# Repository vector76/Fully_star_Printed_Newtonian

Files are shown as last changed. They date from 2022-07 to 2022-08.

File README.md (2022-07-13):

# Fully* Printed Newtonian
The purpose of this project is to create a low-cost, easy to build, yet high quality starter telescope suitable for beginners, which can be extended with accessories for more advanced stargazing.

The goal is to lower the barrier to entry as much as possible, without sacrificing image quality.

Lowering the barrier to entry is viewed in terms of cost and also minimizing the effort in sourcing materials and assembling.  A parametric design can accommodate many mirror sizes, but depending on the size of mirror that is available (and inexpensive), it may be difficult to purchase a tube of suitable size.  Printing the tube is relatively low-cost, and removes the constraint on finding an existing appropriate tube.  A fully* printed design is not a goal per se, but rather it is a consequence of designing to maximize availability.

Full assembly instructions are available in the included PDF.

The source is being published with a permissive license, and the files are also on Printables.com [here](https://www.printables.com/model/241144).

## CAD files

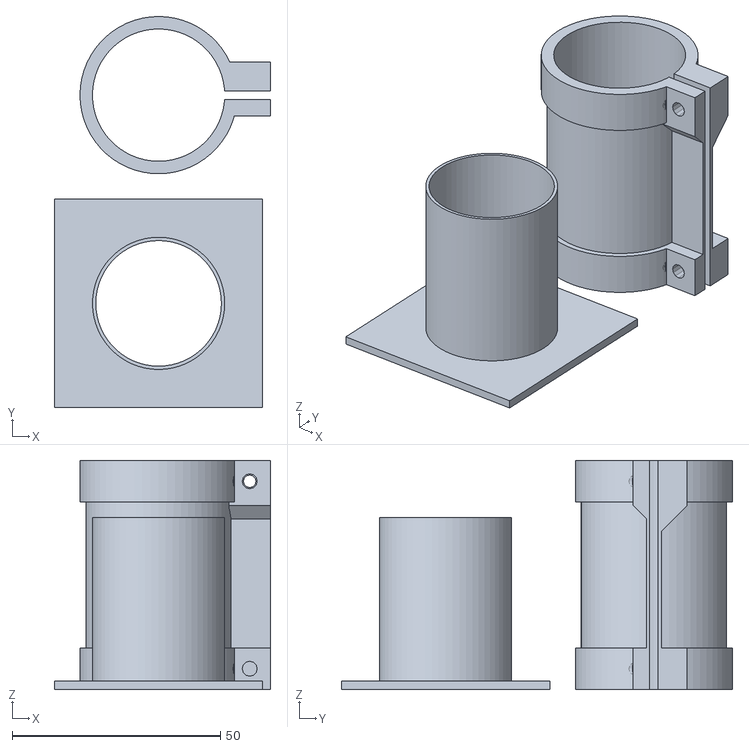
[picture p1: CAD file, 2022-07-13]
Accessories/Focus Estimator.stl
51.9 x 93.9 x 55.0

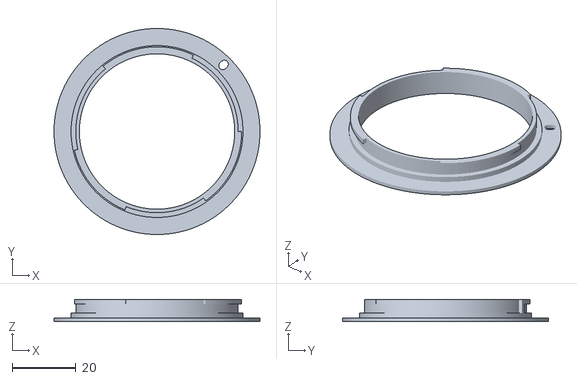
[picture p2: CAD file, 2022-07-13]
Canon_EF_mount_by_thenickdude.stl
64.6 x 64.6 x 6.90

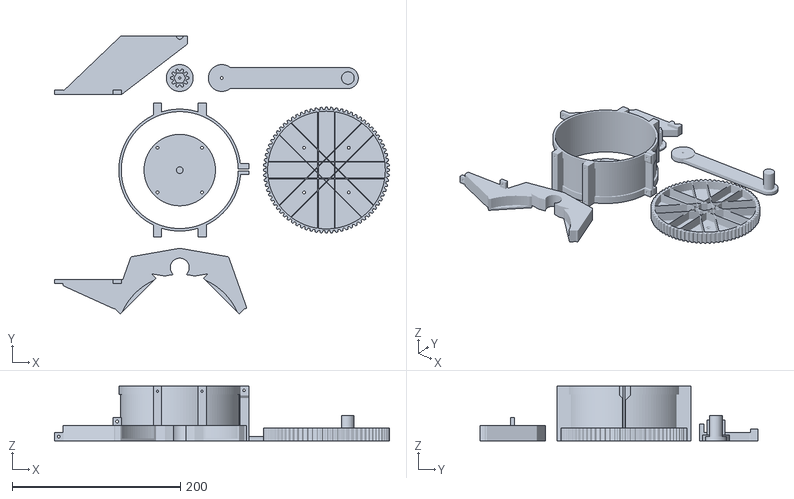
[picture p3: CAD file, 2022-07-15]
D114F900/D114F900 Micro Dobs Print Layout.stl
398.5 x 330.7 x 65.0

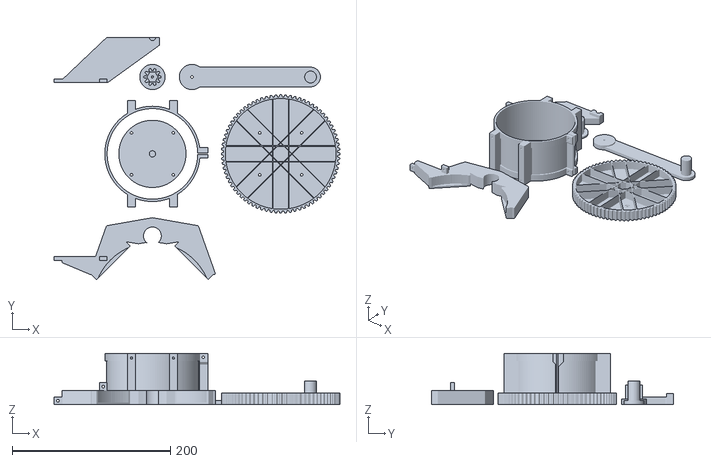
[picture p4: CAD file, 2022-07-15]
D80F800/D80F800 Micro Dobs Print Layout.stl
361.8 x 306.2 x 65.0

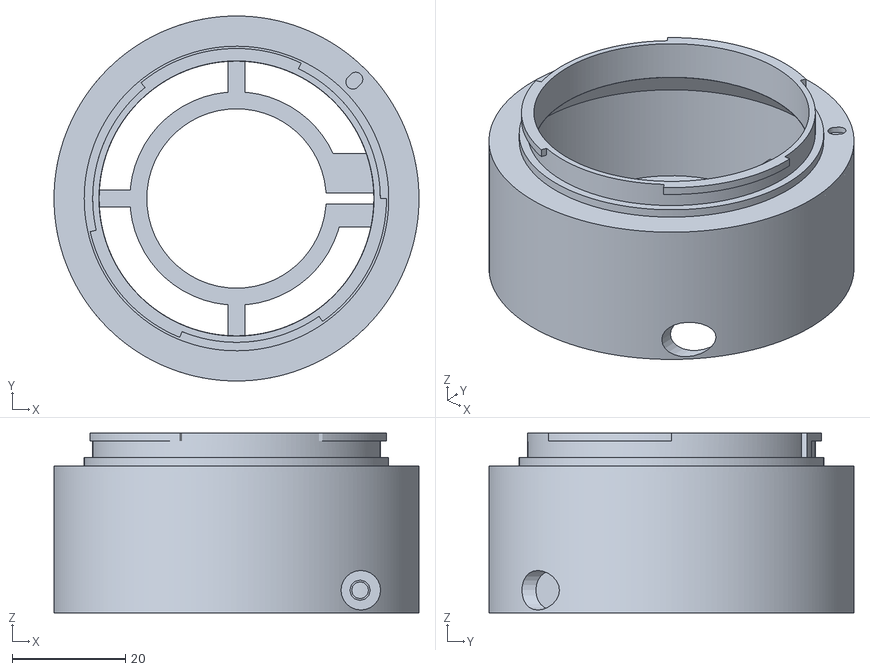
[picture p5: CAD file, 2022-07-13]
Accessories/Canon EF Mount.stl
64.6 x 64.6 x 31.8

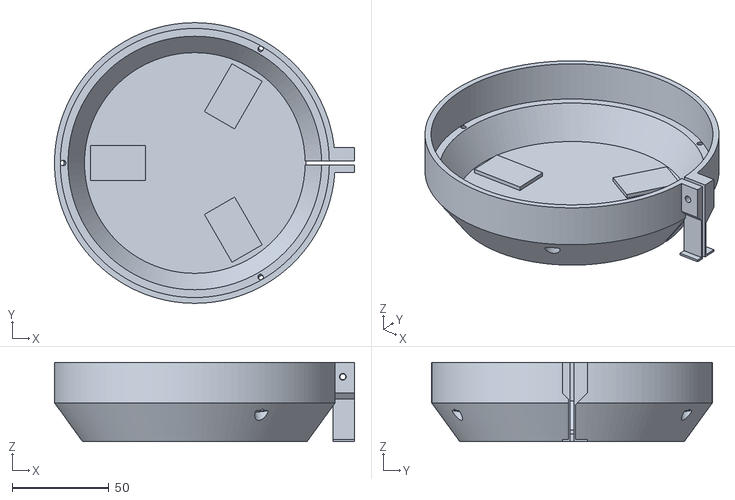
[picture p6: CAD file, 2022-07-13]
D114F900/D114F900 Primary Mount.stl
155.0 x 145.0 x 41.0

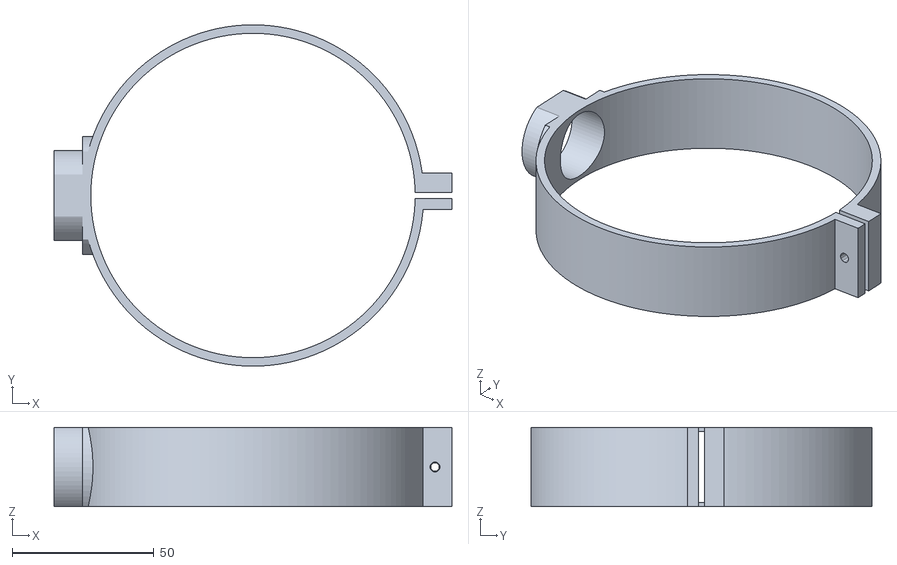
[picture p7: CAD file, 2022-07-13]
D80F800/D80F800 View Mount.stl
140.5 x 120.5 x 28.0

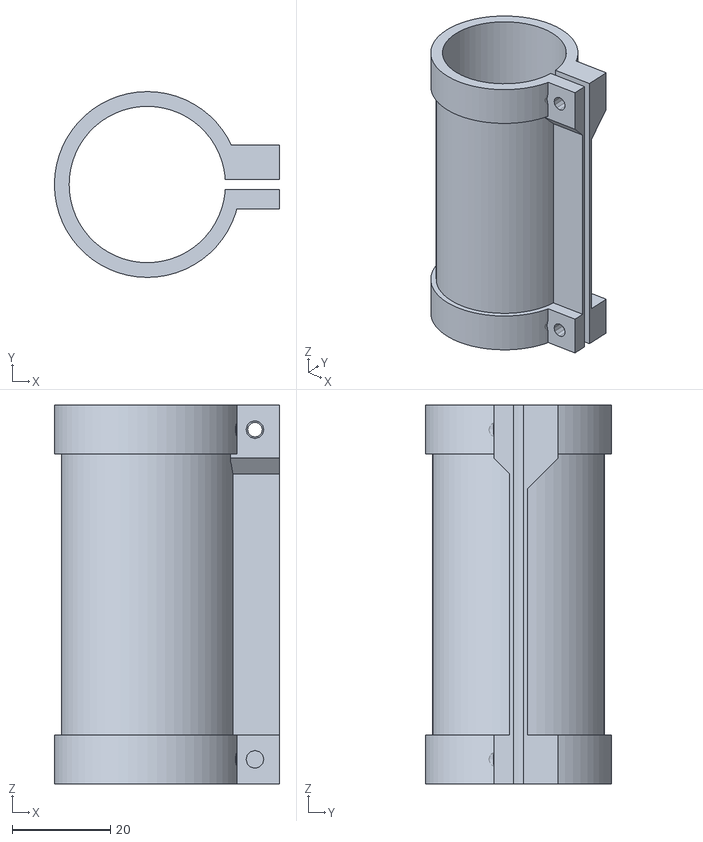
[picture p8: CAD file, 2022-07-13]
Accessories/Eyepiece Mount.stl
45.8 x 37.8 x 77.0

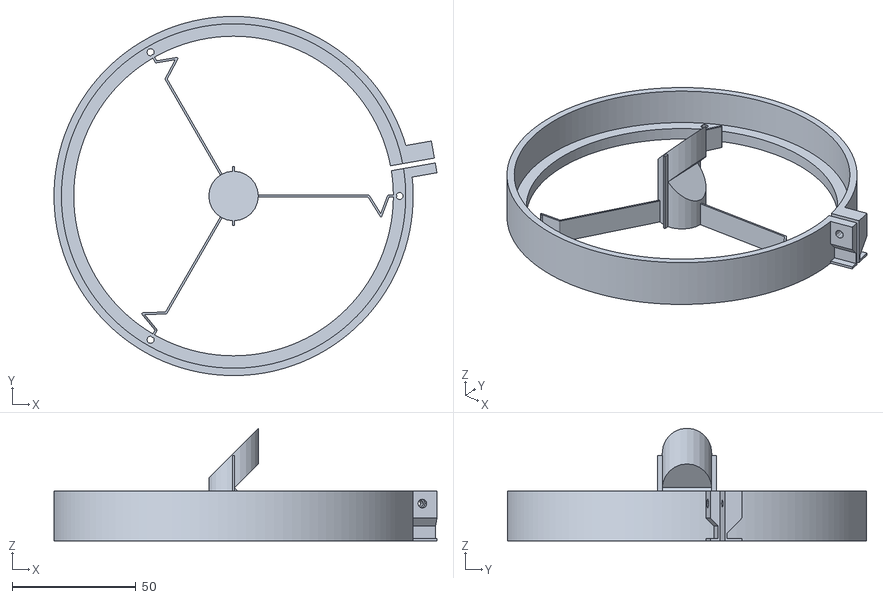
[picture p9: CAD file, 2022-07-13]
D114F900/D114F900 Spider.stl
154.6 x 145.0 x 45.4

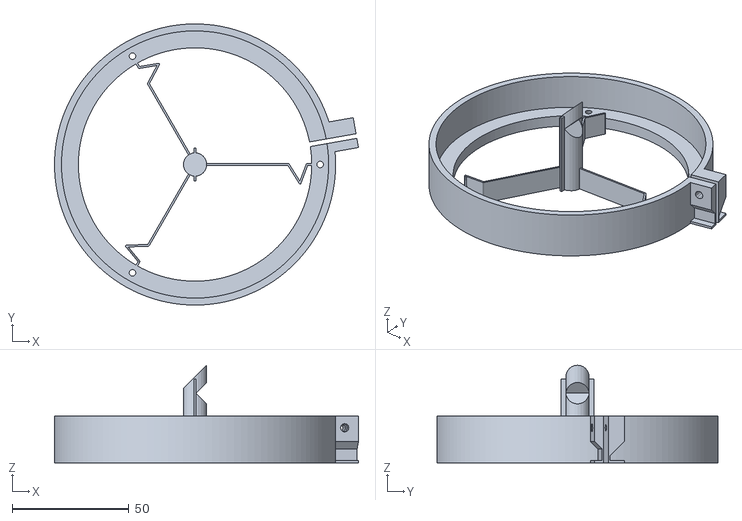
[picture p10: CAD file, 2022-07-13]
D80F800/D80F800 Spider.stl
130.3 x 120.5 x 41.8

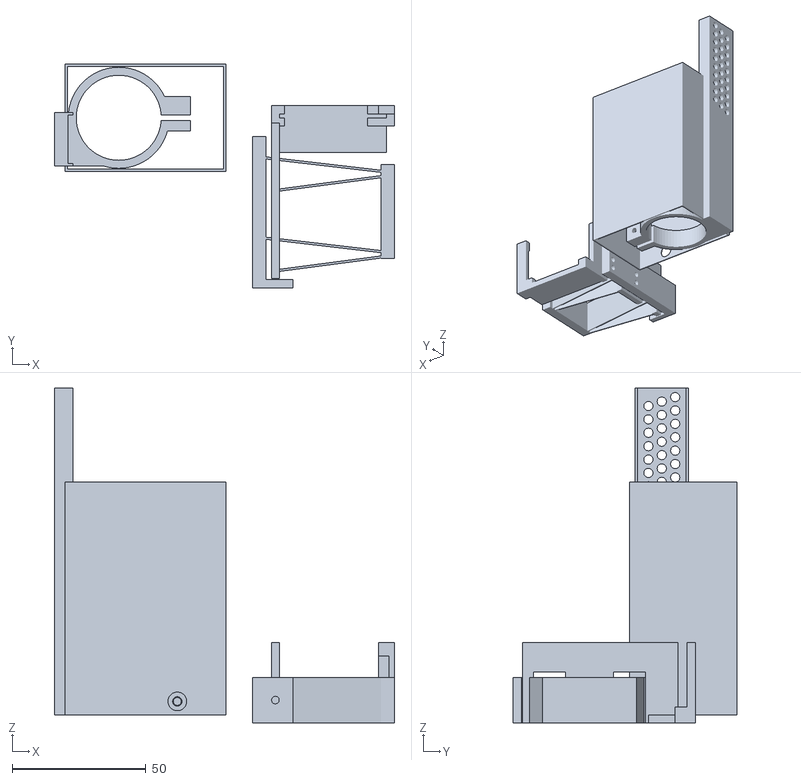
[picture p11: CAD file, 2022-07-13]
Accessories/ESP32-Cam Mount.stl
127.0 x 83.5 x 125.0

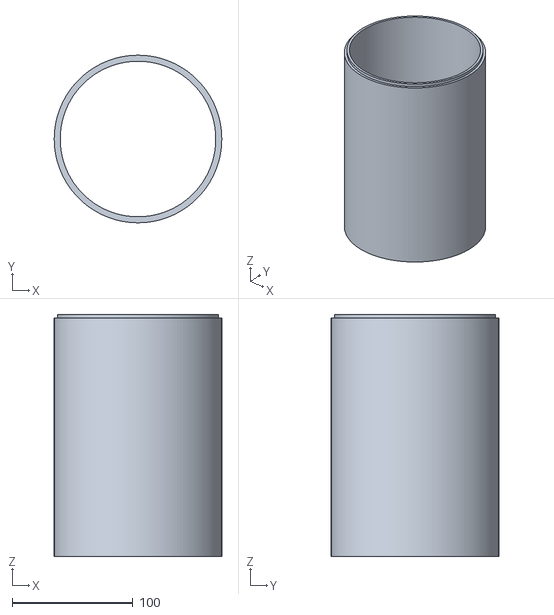
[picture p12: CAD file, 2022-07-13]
D114F900/D114F900 Tube Middle.stl
139.0 x 139.0 x 200.8

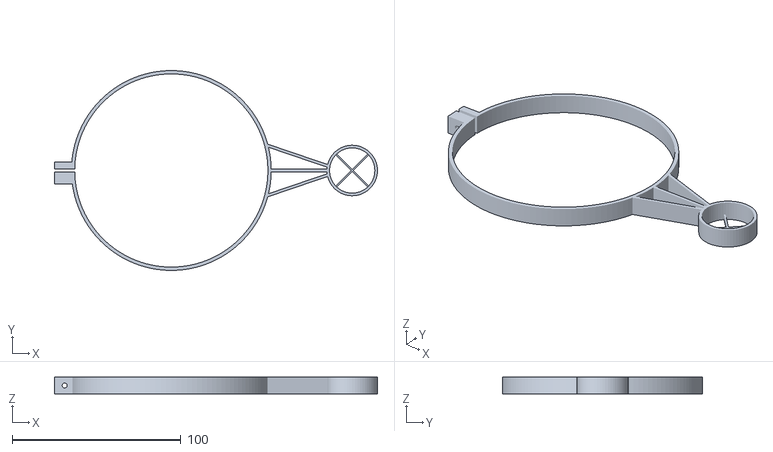
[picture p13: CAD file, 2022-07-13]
D80F800/D80F800 Aiming Reticle.stl
191.5 x 118.5 x 10.0

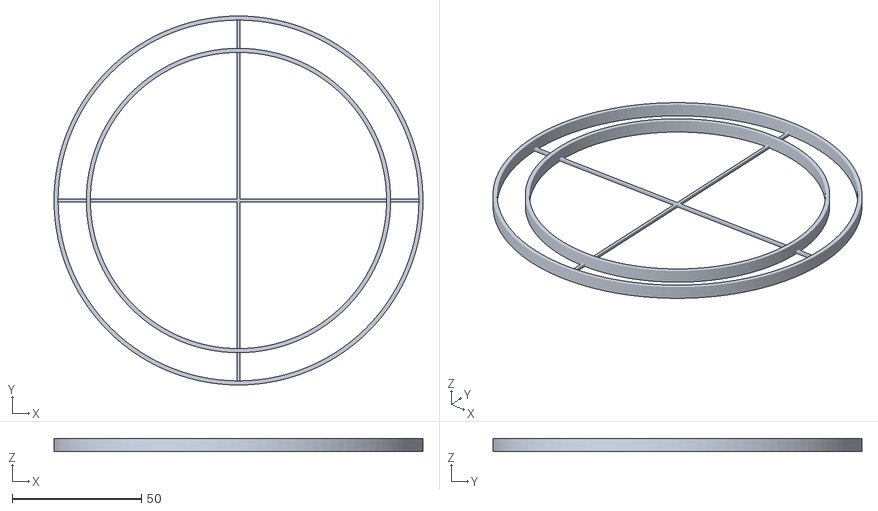
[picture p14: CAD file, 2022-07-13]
D114F900/D114F900 Primary Aligner.stl
142.8 x 142.8 x 5.00

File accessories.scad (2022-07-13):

use <core_parts.scad>  // for ministrap


module primary_crosshairs() {
  wall = 1.6;
  gap = 0.3;
  
  difference() {
    cylinder(d=tube_od+2*gap+2*wall, h=5, $fn=120);
    tz(-0.5) cylinder(d=tube_od+2*gap, h=6, $fn=120);
  }

  // second ring on mirror OD doesn't make a difference with alignment but may be handy
  // for locating the center of the primary.
  difference() {
    cylinder(d=mirror_od+2*gap+2*wall, h=5, $fn=120);
    tz(-0.5) cylinder(d=mirror_od+2*gap, h=6, $fn=120);
  }
  
  for (a=[0, 90]) rotate([0, 0, a])
  tz(0.6) cube([tube_od+1*gap+wall, 1, 1.2], center=true);
}


// secondary crosshairs not really necessary
module secondary_crosshairs() {
  sec_od = 1.25*25.4;
  
  wall = 1.6;
  gap = 0.3;
  
  difference() {
    cylinder(d=sec_od+2*gap+2*wall, h=5, $fn=120);
    tz(-0.5) cylinder(d=sec_od+2*gap, h=6, $fn=120);
  }
  
  for (a=[0, 90]) rotate([0, 0, a])
  tz(0.4) cube([sec_od+1*gap+wall, 1, 0.8], center=true);
}


module EF_mount(clamph=8, mount_depth=ef_mount_depth) {
  efraised = mount_depth-44 - 1;
  // focus is 44.0 mm behind the flange of the mount
  // make it slightly short to allow it to move 1mm closer
  
  // strap
  ministrap(strap_w=clamph);
  // legs
  for (a=[-90, 0, 90]) rotate([0, 0, a]) translate([-32, -1.5, 0]) cube([14, 3, clamph]);

  // ef mount, raised, with a hole for screw access
  difference() {
    EF_mount_raised(h=efraised);
    translate([22, -9, clamph/2]) rotate([90, 0, 0]) cylinder(d=7, h=100, $fn=24);
  }
}


module EF_mount_raised(h=5) {
  wall = 2;
  translate([0, 0, h]) import("Canon_EF_mount_by_thenickdude.stl");

  // slope downward from x=24.3, y=h-1.05 by y=-x+24.3+h-1.05 at x=32.3-wall
  vy = max(0, -32.3+wall+24.3+h-1.05);
  
  difference() {
    union() {
      // %cylinder(d=64.6, h=h-0.95, $fn=120);
      rotate_extrude($fn=200)
      polygon([[32.3-wall, 0], [32.3, 0], [32.3, h-1.05], [24.3, h-1.05], [32.3-wall, vy]]);
    }
    translate([0, 0, -0.5]) cylinder(d=48.6, h=h, $fn=120);
  }
}


module focus_estimator(ht=(mount_length-13)*2/3) {
  w = 0.8;  // thinner than strap so they clamp independently
  tube_d = 25.4*1.25;  // base and eyepiece are same diameter
  
  difference() {
    union() {
      translate([-25, -25, 0]) cube([50, 50, 2]);
      cylinder(d=tube_d, h=ht, $fn=60);
    }
    translate([0, 0, -0.5]) cylinder(d=tube_d-2*w, h=ht+5+1, $fn=60);
  }
}



// work in progress, not ready for release
module eyepiece_fine_adjust(ht=flange_to_focus) {
  // ht is the height above the base where the focus is located
  w = 1.6;  // thinner than strap so they clamp independently
  tube_d = 25.4*1.25;  // base and eyepiece are same diameter
  
  wing_w = 15;
  wing_l = 60+tube_d/2;
  wing_th = 0.6;
  neutral = 6;
  
  // bottom part
  translate([wing_l, wing_l+wing_w+15, 0]) {
    ministrap(id=tube_d);
    
    difference() {
      union() {
        // wings
        for (a=[60, 180, -60]) rotate([0, 0, a]) {
          translate([0, -wing_w/2, 0]) cube([wing_l+1, wing_w, wing_th]);
          // block at end
          translate([wing_l, -wing_w/2, 0]) cube([10, wing_w, neutral+2]);
        }
        // block for deflecting flexure
        rotate([0, 0, -120]) translate([0, -5, 0]) cube([tube_d/2+20, 10, 6]);
      }
      
      // bore out id again
      tz(-0.5) cylinder(d=tube_d, h=11, $fn=60);
      for (a=[60, 180, -60]) rotate([0, 0, a]) {
        // holes in wings
        translate([wing_l+5, 0, -0.5]) cylinder(d=2.9, h=neutral+3, $fn=12);
        // 2mm recess for top part
        translate([wing_l, -5, neutral]) cube([11, 10, 10]);
        translate([wing_l+1-10, -wing_w/2-0.5, neutral]) cube([10, wing_w+1, 10]);
      }
    }
  }
    
  // top part
  // upper strap 10mm shorter than fixed eyepiece
  translate([0, 0, ht-5-10]) ministrap(id=tube_d, feetht=support_free ? ht-5-10 : 0);
  
  // wings and 
  difference() {
    union() {
      // tube
      cylinder(d=tube_d+2*w, h=ht+5-10, $fn=60);
      // bottom reinforcement
      cylinder(d=tube_d+6, h=3, $fn=60);
      // wings
      for (a=[60, 180, -60]) rotate([0, 0, a]) {
        // flexure
        translate([0, -wing_w/2, 0]) cube([wing_l+1, wing_w, wing_th]);
        // block at end for attachment
        translate([wing_l, -10/2, 0]) cube([10, 10, 5]);
      }
      // block for deflecting flexure
      rotate([0, 0, -120]) translate([0, -5, 0]) cube([tube_d/2+20, 10, 6]);
    }
    // bore out inside diameter
    translate([0, 0, -0.5]) cylinder(d=tube_d, h=ht+5+1, $fn=60);
    // cut strap
    strap_slice(ht=ht+5+1);
    // holes in wings
    for (a=[60, 180, -60]) rotate([0, 0, a]) translate([wing_l+5, 0, -0.5]) cylinder(d=3.5, h=6, $fn=12);
    // hole for deflecting flexure
    rotate([0, 0, -120]) translate([tube_d/2+15, 0, -0.5]) cylinder(d=2.9, h=10, $fn=12);
  }
}


module esp32_cam_adapter_mount(nominal_ht=mount_length-3) {
  tube_d = 25.4*1.25;  // base diameter
  hole_offset = 8;  // shift holes to the side
  sup_w = 17;
  tower_ht = nominal_ht + 50;
  
  // strap to grab view mount boss
  ministrap(id=tube_d);
  
  // tower and rectangluar light baffle
  difference() {
    union() {
      // tower
      translate([-19-5, -20/2-hole_offset, 0]) {
        cube([5, 20, tower_ht]);  // main tower
        cube([20, 20, 10]); // foot connection to ministrap
        // guides to prevent offset installlation
        for (y=[0, 19]) translate([0, y, 0]) cube([7, 1, tower_ht]);
      }
      // baffle
      for (x=[-20, 40-0.8]) translate([x, -20, 0]) cube([0.8, 40, nominal_ht+15]);
      for (y=[-20, 20-0.8]) translate([-20, y, 0]) cube([60, 0.8, nominal_ht+15]);
    }
    
    // perforations
    for (yi=[-1, 0, 1])
    for (z=[nominal_ht:5:tower_ht-5])
    translate([-19-6, yi*5-hole_offset, z+yi*5/3]) rotate([0, 90, 0]) 
    cylinder(d=3.5, h=12, $fn=12);

    // bore out space for boss again
    translate([0, 0, -0.5]) cylinder(d=tube_d, h=26, $fn=60);
    
    // access hole for screw
    translate([tube_d/2+6, 0, 5]) rotate([90, 0, 0]) cylinder(d=7, h=50, $fn=30);
  }
  
  %translate([0, 0, nominal_ht]) rotate([-90, 0, 0]) translate([-9, -4, -27/2]) esp32_cam_adapter_flexure();
}


module esp32_cam_adapter_flexure() {
  ht=30;
  tube_d = 25.4*1.25;  // base diameter
  cam_w = 27;
  cam_l = 40;
  cam_ypos = 9;  // camera center is 9mm from one end, centered along width
  
  cam_th = 1.5;
  slot_depth = 3;
  slot_end = 2;
  slot_end2 = 7;
  flex_th = 0.8;
  
  sup_w = 17;
  flex_ht = sup_w; // cam_w/2;
  flex_x = cam_l-2;
  
  hole_offset = 8;  // shift holes downward
  
  // bottom below camera
  translate([0, -3-10, -3]) cube([cam_l, 10+6+cam_th, 3]);
  
  difference() {
    union() {
      translate([-3, -3, -3]) cube([3+slot_end, 6+cam_th, 3+slot_depth]);
      translate([cam_l-slot_end2,-3,-3]) cube([slot_end2+3, 6+cam_th, 3+slot_depth]);
    }
    cube([cam_l, cam_th, cam_w]);
  }
  
  // vertical stem
  translate([cam_l-3, cam_th, 0]) difference() {
    cube([6, 3, cam_w]);
    // cavity so it doesn't jam in the middle and skew it
    translate([-0.1, -0.5, 3]) cube([4, 1.5, cam_w-8]);
  }
  
  // intermediate
  translate([flex_x, -50-2.5, -3]) cube([5, 35, flex_ht]);
  
  for (y=[-20, -50]) {
    // stage 1 flexures
    hull() {
      translate([flex_x, y, -3]) cylinder(d=flex_th, h=flex_ht, $fn=36);
      translate([-5, y+5, -3]) cylinder(d=flex_th, h=flex_ht, $fn=36);
    }
    
    // stage 2 flexures
    hull() {
      translate([flex_x, y-2, -3]) cylinder(d=flex_th, h=flex_ht, $fn=36);
      translate([0, y-7, -3]) cylinder(d=flex_th, h=flex_ht, $fn=36);
    }
  }
  
  // final stage of flexure?
  difference() {
    translate([-3, -50-10, -3]) cube([3, 58, cam_w+3]);
    for (y=[-20, -50]) translate([-3.5, y-6, -3.1]) cube([6, 12, flex_ht+2.1]);
  }
  
  // support and holes for mounting screw
  difference() {
    translate([-10, -62, -3]) cube([5, 55, sup_w]);
    for (zi=[-1, 0, 1])
    for (y=[-30, -10]) translate([-11, y, cam_w/2+zi*5-hole_offset]) 
      rotate([0, 90, 0]) cylinder(d=2.9, h=12, $fn=12);
  }
  
  // top ledge and spot for focus adjustment screw
  translate([-10, -62-1.5, -3])
  difference() {
    cube([15, 3, sup_w]);
    translate([8.5, -1, flex_ht/2]) rotate([-90, 0, 0]) cylinder(d=2.9, h=10, $fn=12);
  }
  
  
  // top diving board and focus adjustment screw
  *difference() {
    translate([-10, -55-5, -3]) cube([cam_l+10+2+5, 5, cam_w-1]);
  
    translate([cam_l+2+2.5, -61, (cam_w-1)/2-3])
    rotate([-90, 0, 0]) cylinder(d=2.9, h=12, $fn=12);
  }
  
  // visualize board and camera
  %cube([cam_l, cam_th, cam_w]);
  %translate([cam_ypos, cam_th, cam_w/2]) 
  rotate([-90, 0, 0]) cylinder(d=8, h=8, $fn=24);
  
  // from center of camera to surface of support plate is 19 mm.
  // focal plane is about 4mm from back surface
  // so focal plane to mounting hole is about 34 mm
  // with focus about 30mm above base, we need 64 mm from base to mounting hole

}

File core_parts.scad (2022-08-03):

module assembled() {
  %cylinder(d=tube_od, h=tube_length);
  primary_mount();
  
  translate([0, 0, tube_length/2]) rotate([0, 0, 180]) tripod_strap();
  
  tz(tube_length) rotate([180, 0, 0]) spider();
  
  tz(secondary_distance-7.5-primary_setback) image_base_strap();
  
  for (z=[tube_length*0.1, tube_length*0.7])
  tz(z) rotate([0, 0, 140]) test_strap_aiming();
}


module all_part_layout() {
  layout = tube_od+15;

  translate([0, 0, mirror_thickness+7])
  r45() primary_mount();

  translate([0, layout, 5]) r45() spider();

  translate([-layout, 0, 12.5]) r45() tripod_strap();

  // for testing strap design and fit with OD
  // translate([layout, 0, 0]) r45() test_strap_aiming();

  translate([-layout, layout, 0]) r45() image_base_strap();

  translate([-layout, layout, 0]) eyepiece_tube();
}


module eyepiece_tube(ht=flange_to_focus, extra=0) {
  // ht is the height above the base where the focus is located
  w = 1.6;  // thinner than strap so they clamp independently
  tube_d = 25.4*1.25;  // base and eyepiece are same diameter
  
  // two straps
  ministrap(id=tube_d);
  translate([0, 0, ht-5]) ministrap(id=tube_d, feetht=support_free ? ht-15 : 0);
  
  // tube to connect them
  difference() {
    cylinder(d=tube_d+2*w, h=ht+5+extra, $fn=60);
    translate([0, 0, -0.5]) cylinder(d=tube_d, h=ht+5+extra+1, $fn=60);
    strap_slice(ht=ht+5+extra+1);
  }
  
}


module ministrap(id=25.4*1.25, wall=3, strap_w=10, slice_w=2, feetht=0) {
  feetw = 0.8;
  difference() {
    union() {
      cylinder(d=id+2*wall, h=strap_w, $fn=60);
      
      difference() {
        // block for clamping
        translate([id/2+wall-2, -5, -feetht])
          cube([10, 13, strap_w+feetht]);
        
        // remove feetht from bottom but only from the clamping block
        if (feetht > 0) {
          hull() for (dy=[0, 10])
          translate([id/2+wall-2.5, slice_w/2+feetw+dy, -feetht-dy-20])
          cube([13, 1, feetht+2*dy-7+20]);
          
          mirror([0, 1, 0]) hull() for (dy=[0, 10])
          translate([id/2+wall-2.5, slice_w/2+feetw+dy, -feetht-dy-20])
          cube([13, 1, feetht+2*dy-4+20]);
        }
      }
    }
    
    // bore
    translate([0, 0, -0.5]) cylinder(d=id, h=strap_w+1, $fn=60);
    
    // slice for clamping
    strap_slice(ht=strap_w+1+feetht, slice_w=slice_w);
    
    // screw holes for clamping
    translate([id/2+wall+3, 0, strap_w/2]) {
      rotate([90, 0, 0]) cylinder(d=3.6, h=12, $fn=12);
      rotate([-90, 0, 0]) cylinder(d=3, h=12, $fn=12);
      translate([0, -5.1, 0]) rotate([90, 0, 0]) cylinder(d=8, h=12, $fn=24);
    }    
  }
  
}


module r45() {
  rotate([0, 0, 45]) children();
}


module image_base_strap() {
  //sw = 15;  // width of thick part of strap
  //tw = 6;  // extra thin width added top and bottom
  sw = 28;
  tw = 0;
  st = 3;  // strap thickness (thick part)
  tl = 10;  // part of tube for grabbing
  
  difference() {
    union() {
      strap(wall=st, strap_w=sw, thinbot=tw, feetht=support_free ? tw : 0);
  
      translate([-tube_od/2-10-st, 0, sw/2])
      rotate([0, 90, 0]) {
        cylinder(d=31.75, h=tl+st, $fn=60);
        // flange provides decent flat surface rather than relying on tube od
        translate([0, 0, tl]) cylinder(d=41.75, h=st+5, $fn=60);
      }
    }
    
    // inside tube bore
    translate([0, 0, -tw-0.5]) cylinder(d=tube_od, h=sw+2*tw+1, $fn=120);
    
    // bore in tube
    translate([-tube_od/2-10-4, 0, sw/2]) 
    rotate([0, 90, 0])  cylinder(d=25, h=20, $fn=60);
    
    // cut off top and bottom
    for (z=[sw+tw, -50-tw]) translate([0,0,z]) cylinder(d=tube_od+2*tl+2*st+10, h=50);
  }
  
  %translate([-tube_od/2-3, 0, sw/2]) rotate([0, -90, 0]) eyepiece_tube();
}


module test_strap_aiming() {
  dist = 50;  // distance from OD of tube
  rib_w = 1.6;
  ring_od = 30;
  ring_r = ring_od/2;
  ring_th = 1.6;
  
  rotate([0, 0, 180]) strap(wall=2);
  
  difference() {
    union() {
      // three ribs support the ring
      for (a=[0, 15, -15]) hull() {
        rotate([0, 0, a]) 
        translate([tube_od/2+1, 0, 0]) cylinder(d=rib_w, h=10, $fn=24);
        translate([tube_od/2+dist-ring_r+1, a/6, 0]) cylinder(d=rib_w, h=10, $fn=24);
      }
      
      translate([tube_od/2+dist, 0, 0])
      cylinder(d=ring_od, h=10, $fn=60);
    }
    
    translate([tube_od/2+dist, 0, -0.5])
    cylinder(d=ring_od-2*ring_th, h=11, $fn=60);
  }
  
  // crosshairs
  translate([tube_od/2+dist, 0, 0]) for (a=[-45, 45]) rotate([0, 0, a])
  translate([-ring_r, -0.4, 0]) cube([ring_od, 0.8, 3]);
}

module strap_slice(ht=11, slice_w=2) {
  // slice ring and maybe other stuff
  translate([0, -slice_w/2, -ht]) cube([300/2+21, slice_w, 2*ht]);
}


module strap(wall=3, strap_w=10, clamp_extra=0, slice_w=2, extrabot=0, thinbot=0, feetht=0) {
  strap_mid = strap_w/2;
  thinw = 0.8;
  feetw = 0.8;
  
  // main strap
  difference() {
    union() {
      // main ring grips outside of tube
      hull() {
        translate([0, 0, -extrabot])
        cylinder(d=tube_od+2*wall, h=strap_w+extrabot, $fn=120);
      
        if (thinbot > 0) translate([0, 0, -extrabot-wall])
        cylinder(d=tube_od+2*thinw, h=strap_w+extrabot+2*wall, $fn=120);
      }
      
      if (thinbot > 0)
        translate([0, 0, -thinbot])
        cylinder(d=tube_od+2*thinw, h=strap_w+2*thinbot, $fn=120);
      
      difference() {
        // block for clamping, 5 one side, 8 other side, not counting slice
        translate([tube_od/2+wall-1, -5-clamp_extra, -feetht]) 
          cube([11, 13+clamp_extra, strap_w+feetht]);

        // remove feetht from bottom but only from the clamping block
        if (feetht > 0) {
          hull() for (dy=[0, 10])
          translate([tube_od/2+wall-1.5, slice_w/2+feetw+dy, -feetht-dy-20])
          cube([12, 1, feetht+2*dy-7+20]);
          
          mirror([0, 1, 0]) hull() for (dy=[0, 10])
          translate([tube_od/2+wall-1.5, slice_w/2+feetw+dy, -feetht-dy-20])
          cube([12, 1, feetht+2*dy-4+20]);
        }
      }
      
      if (feetht > 0) {
        translate([tube_od/2+wall-1, -5, -feetht]) 
        cube([11, 13, 1]);
      }
    }

    // bore for tube
    translate([0, 0, strap_mid-extrabot/2]) {
      cylinder(d=tube_od, h=strap_w+extrabot+2*thinbot+1, center=true, $fn=120);
    }

    // slice for clamping
    strap_slice(ht=strap_w+1+thinbot+extrabot+feetht, slice_w=slice_w);

    // screw holes for clamping
    translate([tube_od/2+wall+4, 0, strap_mid]) {
      rotate([90, 0, 0]) cylinder(d=3.6, h=12, $fn=12);
      rotate([-90, 0, 0]) cylinder(d=3, h=12, $fn=12);
      translate([0, -5.1, 0]) rotate([90, 0, 0]) cylinder(d=8, h=12, $fn=24);
    }
    
  }
}


module tripod_strap() {
  wall = 3;
  strap_w = 15;
  strap_mid = strap_w/2;
  block_len = 40;
  block_w = 39;
  block_th = 6.8;  // about 1.2 mm thick behind nut
  clamp_extra = 2;
  
  botamt = (block_len-strap_w)/2;
  
  difference() {
    union() {
      // strap included so bolt can be subtracted also
      rotate([0, 0, 130])
      strap(strap_w=strap_w, clamp_extra=clamp_extra, thinbot=botamt, feetht=support_free ? botamt : 0);
  
      // tripod block (silghtly wide to attach other blocks
      translate([-block_th-tube_od/2, -block_w/2-0.5, -block_len/2+strap_mid])
      cube([block_th+5, block_w+1, block_len]);
      
      *for (i=[0,1]) mirror([0, i, 0])
      translate([-tube_od/2-block_th-4, block_w/2, -block_len/2+strap_mid])
      cube([14, 3, block_len]);
    }
    
    // bore for tube (leaves material at ends of tripod block)
    translate([0, 0, strap_mid]) {
      cylinder(d=tube_od, h=block_len-8, center=true, $fn=120);
      cylinder(d=tube_od-0.6, h=block_len+1, center=true, $fn=120);
    }
    
    // pocket for 1/4-20 nut
    translate([-tube_od/2-5.6, 0, strap_mid]) rotate([0, 90, 0])
    cylinder(d=12.9, h=10, $fn=6);  // plenty tall, reaches inward
    
    // hole for 1/4-20 screw
    translate([-tube_od/2-block_th-0.5, 0, strap_mid]) rotate([0, 90, 0])
    cylinder(d=25.4/4, h=block_th+5, $fn=24);
    
  }
}


// front end holds secondary mirror
module spider() {
  stem_length = hole_from_end-secondary_thickness*sqrt(2);
  stem_d = secondary_size-5;
  spar_w = 0.8;
  base = 5;

  // strap for grabbing tube, extends downward to join with additional ring
  rotate([0, 0, 10])
  tz(5) strap(extrabot=base+5, feetht=support_free ? 5+5 : 0);
  
  difference() {
    translate([0, 0, -base]) cylinder(d=tube_od+1, h=base, $fn=120);
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

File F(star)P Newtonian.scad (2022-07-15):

// Which part(s) to show
part = "Assembled";  // [ "Primary Mount", "Spider", "View Mount", "Tripod Strap", "Assembled", "Parts Flat", "Primary Aligner", "Aiming Reticle", "Eyepiece Mount", "Canon EF Mount", "Focus Estimator", "ESP32-Cam Mount", "Tube Bottom", "Tube Middle", "Tube Top", "Tube Demonstration", "Micro Dobs Assembled", "Micro Dobs Print Layout" ]
// Diameter of primary mirror (mm)
mirror_od = 114;
// Focal length (mm)
mirror_focal_length = 900;
// Thickness of primary mirror (mm)
mirror_thickness = 14; // 0.1
// Minor diameter of secondary mirror (mm)
secondary_size = 25;
// Thickness of secondary mirror (mm)
secondary_thickness = 5; // 0.1
// Purchased tube or printed?
tube_source = "Printed"; // [ Printed, Purchased ]
// Adjust model so supports are mostly unnecessary?
support_free = true;

/* [Printed Tube Options] */
// Maximum Z height of tube segments (mm)
max_print_ht = 210;

/* [Purchased Tube Parameters] */
// Inside diameter of purchased tube (mm)
purchased_tube_id = 89.2;
// Outside diameter of purchased tube (mm)
purchased_tube_od = 76.3;

module customizer_stop() {}

/* [Accessory Parameters] */
// Flange to focal distance
ef_mount_depth = 71; // 0.1

// Common variables for both tube and parts
part2 = "";
part_ = part2 == "" ? part : part2;  // override part with part2

// intended size of output projected image (magnification depends on focal length)
fov_size = 15;
// tube must be larger than mirror or it will block some of field of view
tube_id = tube_source == "Purchased" ? purchased_tube_id : mirror_od + fov_size;
// outer diameter
tube_od = tube_source == "Purchased" ? purchased_tube_od : tube_id + 2*5;
// thickness of tube wall
tube_wall = (tube_od-tube_id)/2;
// front of primary is this far back from end of tube (for length purposes)
primary_setback = 2;
// the strap for attaching stuff is this wide
mount_strap_width = 35;
// in front of mount strap, leave this much for the spider to grab onto
spider_clip_allowance = 20;
// center of side hole distance from tube front end
hole_from_end = spider_clip_allowance + mount_strap_width/2;
// size of hole matches mount strap
hole_size = 25;
// focus is this radial distance from outside of tube
mount_length = 75;
// focus is this distance from center of tube
focus_total_radius = mount_length + tube_wall + tube_id/2;
// distance from primary mirror to center of secondary
secondary_distance = mirror_focal_length - focus_total_radius;
// total tube length after assembly
tube_length = secondary_distance - primary_setback + mount_strap_width/2 + spider_clip_allowance;
// distance from mounting flange to focal plane (3 is thickness of flange)
flange_to_focus = mount_length - 3;

// These items are specific to the tube generation:

// joint between tubes overlaps by this much (tiny bit needed just for alignment)
joint_overlap = 3;
// number of tube sections given maximum printable Z
tube_sections = ceil(tube_length / (max_print_ht-joint_overlap));
// section effective length (excludes overlap)
section_effective_length = tube_length/tube_sections;
// number of facets (and internal corrugations)
p = floor(tube_id*PI/(tube_wall-1.2)*sqrt(2)/2)*2;

// Guidance for the user, printed or purchased:

echo("###########################################");
if (tube_source == "Purchased") {
  echo(str(" Cut tube to length: ", str(tube_length), " mm"));
  echo(str(" Hole center this far from end: ", str(mount_strap_width/2+spider_clip_allowance), " mm"));
  echo(str(" Hole diameter: ", str(hole_size), " mm"));
}
else {
  echo(str(" Printed tube total length: ", tube_length, " mm"));
  echo(str(" Printed tube outside diameter: ", tube_od, " mm"));
  echo(str(" Printed tube section height (excluding top lip):", section_effective_length, " mm"));
  echo(str(" Total number of tube segments: ", tube_sections));
}
echo("###########################################");

// Implementation below here
include <tube_modules.scad>
include <core_parts.scad>
include <accessories.scad>
include <micro_dobs_mount.scad>

// Core parts
if (part_ == "Primary Mount") { primary_mount(); }
if (part_ == "Spider") { spider(); }
if (part_ == "View Mount") { image_base_strap(); }
// Additional parts for main tube
if (part_ == "Tripod Strap") { tripod_strap(); }
if (part_ == "Alignment Guide") { test_strap_aiming(); }
// Some layouts/visualization?
if (part_ == "Assembled") { rotate([0, 45, 0]) tz(-tube_length/2) assembled(); }
if (part_ == "Parts Flat") { all_part_layout(); }
// Accessories
if (part_ == "Primary Aligner") { primary_crosshairs(); }
if (part_ == "Aiming Reticle") { test_strap_aiming(); }
// if (part == "Secondary Aligner") { secondary_crosshairs(); }
if (part_ == "Focus Estimator") { translate([0, 50, 0]) eyepiece_tube(ht=mount_length*2/3);  
    focus_estimator(); }
if (part_ == "Eyepiece Mount") { eyepiece_tube(); }
//if (part == "Eyepiece Mount w/ Fine Adjustment") { eyepiece_fine_adjust(); }
if (part_ == "Canon EF Mount") { EF_mount(); }
if (part_ == "ESP32-Cam Mount") { esp32_cam_adapter_mount(); 
  translate([60, 0, 0]) esp32_cam_adapter_flexure(); }
// Printed tubes
if (part_ == "Tube Top") { tube_top(); }
if (part_ == "Tube Middle") { tube_mid(); }
if (part_ == "Tube Bottom") { tube_bot(); }
if (part_ == "Tube Demonstration") { difference() { tube_bot(50); tz(25) cylinder(d=500, h=500); } }
// "Micro Dobsonian" mount
if (part_ == "Micro Dobs Assembled") { micro_dobs_assembled(); }
if (part_ == "Micro Dobs Print Layout") { micro_dobs_print_layout(); }

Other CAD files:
D80F800/D80F800 Primary Aligner.stl
D114F900/D114F900 Tripod Strap.stl
D80F800/D80F800 Tripod Strap.stl
D114F900/D114F900 Aiming Reticle.stl
micro_dobs_mount.scad
D114F900/D114F900 Tube Bottom.stl
D114F900/D114F900 Tube Top.stl
D114F900/D114F900 View Mount.stl
D80F800/D80F800 Primary Mount.stl
tube_modules.scad
unwin_modules.scad

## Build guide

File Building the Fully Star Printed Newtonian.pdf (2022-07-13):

# Building the Fully* Printed Newtonian

## Introduction

This document describes the process for selecting sizes and building the “Fully* Printed Newtonian” telescope, which built with only printer filament, mirrors, glue, and #6 screws. (Use of a purchased tube is also an option and is described below.)

The design philosophy and the reasons for certain design choices
are detailed elsewhere, and this document focuses on preparing
the materials, choosing the size, and assembling the telescope.

(The model files are available on Printables.com here (https://www.printables.com/model/241144) and on GitHub here.) (https://github.com/vector76/Fully_star_Printed_Newtonian)

## Materials Required

The printed parts excluding the tube require roughly 250 g of filament (for a 114 mm mirror diameter), at ~100 for the primary mount, and ~50g each for the secondary mount, the viewport mount, and the tripod strap. A bit more will be needed for the various accessories. Black filament should be used to minimize
stray light, although non-black filament may be okay if the
telescope is used only at night.

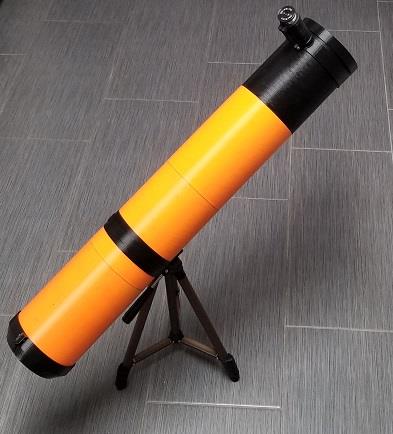
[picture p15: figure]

The tube, if printed, requires about 800 g of filament for the variant with 114 mm diameter, 900 mm focal length. The filament requirement will be roughly proportional to diameter and length. As with the other parts, the tube should be printed with black filament, although it is also possible to paint the interior of the tube.

Excluding the mirror and tube, which are discussed in the next section, you will need:
- Screws: #6 sheet metal screws, 1/2” length, which I believe is equivalent to 3.5 mm sheet metal screws with 12 mm length (length is not critical). You will need at least 6 to install an eyepiece.
- Epoxy
- Tape (optional) for securing mirrors to mounts instead of epoxy

*
Since the Fully* Printed Newtonian is not literally, fully printed, please do not refer to it as “Fully Printed Newtonian” or “FP Newtonian” or “FPN”. Instead call it “Fully* Printed Newtonian” or “F*P Newtonian”, or “F*PN”.

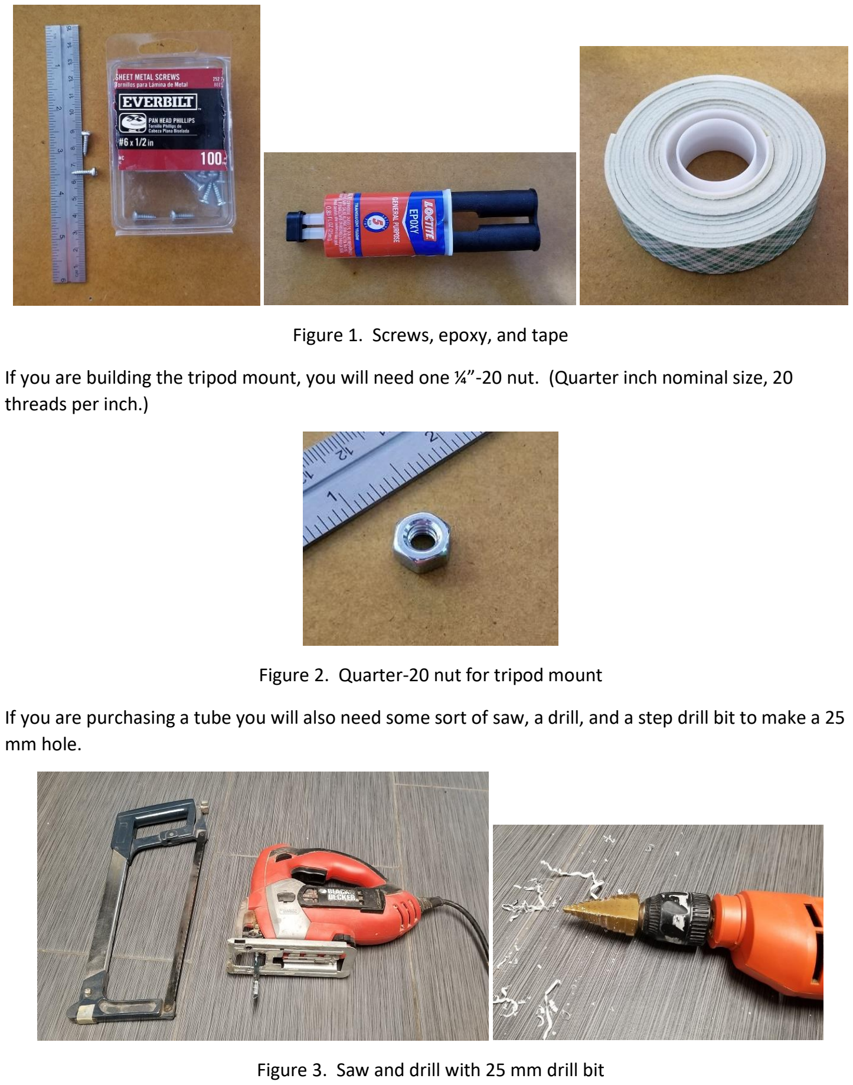
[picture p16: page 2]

Figure 1. Screws, epoxy, and tape

If you are building the tripod mount, you will need one ¼”-20 nut. (Quarter inch nominal size, 20 threads per inch.)

Figure 2. Quarter-20 nut for tripod mount

If you are purchasing a tube you will also need some sort of saw, a drill, and a step drill bit to make a 25 mm hole.

Figure 3. Saw and drill with 25 mm drill bit

## Choice of Mirror and Tube

For a Newtonian style telescope to have ideal performance, there are two options: the primary mirror can be spherical with a relatively long focal ratio, or it must be parabolic. The options are summarized in Figure 4, where the green region represents the zone where spherical mirrors produce good image quality:

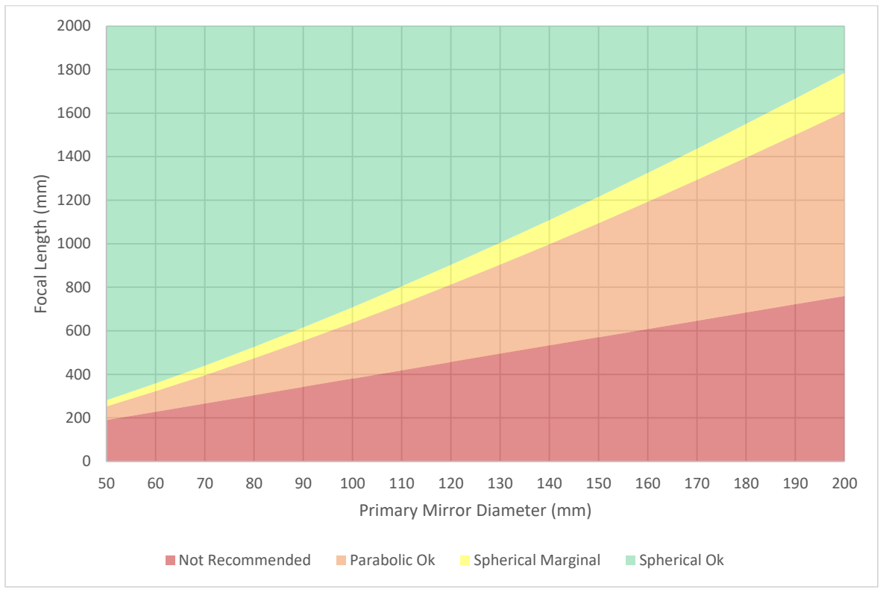
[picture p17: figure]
Focal Length (mm); Primary Mirror Diameter (mm); Not Recommended; Parabolic Ok; Spherical Marginal; Spherical Ok

Figure 4. Cheaper spherical mirrors are permitted at longer focal ratios, while parabolic mirrors are required for shorter focal ratios.

Since spherical mirrors are much less expensive than parabolic mirrors, it is assumed that spherical mirrors with long focal lengths are usually going to be chosen, but parabolic mirrors are also permitted, except that very short focal lengths are not recommended, as illustrated by the red area in Figure 4.

For a printed tube, the outside diameter of the tube is about 25 mm larger than the mirror, and your printer must be able to accommodate this, plus an additional 6 mm for the various straps that clamp onto to the outside of the tube. So, for example, a 150 mm printable area would be able to accommodate a mirror size up to 119 mm.

If you purchase a tube, the recommended size for the inside diameter is between 15 mm and 40 mm larger than the mirror. The exact dimension is not critical, but too large or too small and the performance will suffer. The outside diameter of the tube must be at least 10 mm larger than the diameter of the mirror, or it will not assemble properly.

Given these guidelines, you may purchase a tube and cut it to length if you can find a compatible tube and mirror combination of appropriate sizes, or if you wish to use a mirror for which no appropriate tube can be found (or if you prefer not to use a saw and drill), then you may print a tube instead.

## Constructing Telescope Body from Purchased Tube

Cut the tube such that the length L is

L = focal length − 77 −

tube outside diameter
2

Cut the ends perpendicular and flat to the extent possible. (Note: do not assume the factory-cut end of PVC tube is cut square!) One way to get a square cut is to wrap a ribbon or some flat material like paper around the tube and use it as a guide to mark a line. Then cut the tube very slightly long and use a file or sandpaper to file the tube back to the line.

After cutting the tube to length, drill a hole in the side. This hole should be 25 mm in diameter and the center of the hole should be 37.5 mm from the end.

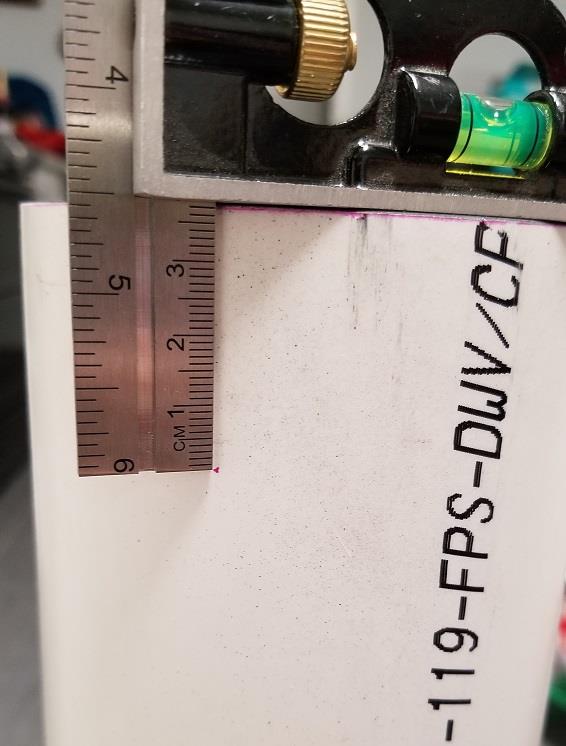
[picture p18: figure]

Figure 5. Side hole is 37 mm from end

The interior of the tube should be painted black, and the inside surface of the drilled hole should also be painted black, to minimize stray light contaminating the image.

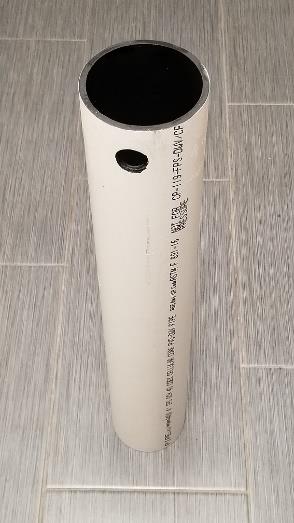
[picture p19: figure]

Figure 6. Painted interior of tube and edge of hole

As an example, for a primary mirror with a diameter of 80 mm and a focal length of 800 mm, the recommended inside diameter is between 95 and 120 mm. A four-inch PVC tube has an inside diameter of approximately 106 mm, so it is suitable for the 80 mm mirror. The outer diameter of the 4” PVC pipe is about 113 mm, so the tube should be cut to a length of:

L = 800 − 77 −

113
2

= 666.5 mm length

Irrespective of mirror or tube diameter or focal length, the hole in the side of the tube should be centered at 37.5 mm from the end, and the diameter should be 25 mm.

## Printing and Assembling the Customized Tube

If an appropriate tube is difficult to find, or if it is expensive, then tubes can be printed. Even if an appropriate tube is available, using a printed tube requires only gluing, and avoids the need to cut it to length or drill holes, which might be an advantage depending on what tools are available.

The printed tube is printed in sections, with one ‘bottom’ segment serving as the first segment, to which the primary mirror is attached, and one ‘top’ segment, where the secondary mirror and viewing attachments are mounted. In between are some number of ‘middle’ segments. Usually there will be two middle segments, but the exact number will depend on the overall length of the final tube and the maximum Z capacity of your printer.

Black filament is recommended, to minimize stray light within the tube. If you are not using black filament, then you should plan on painting the interior surface black. This is even more important if you use the telescope for daytime terrestrial viewing.

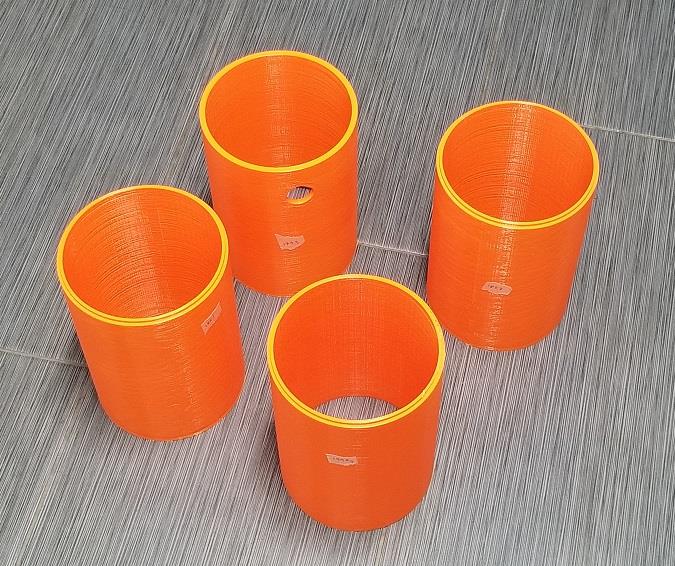
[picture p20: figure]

Figure 7. Printed segments for 114 mm mirror with 900 mm focal length.

The assembly of the segments should be self-evident. Each tube segment has a concentric overlapping feature to assist gluing the segments straight and concentric. Perform a dry fit of all the pieces before gluing. Then apply epoxy to the mating surfaces and press together such that the layer of glue mostly squeezes out and the surfaces are bonded securely and straight. Allow plenty of time for the epoxy to set.

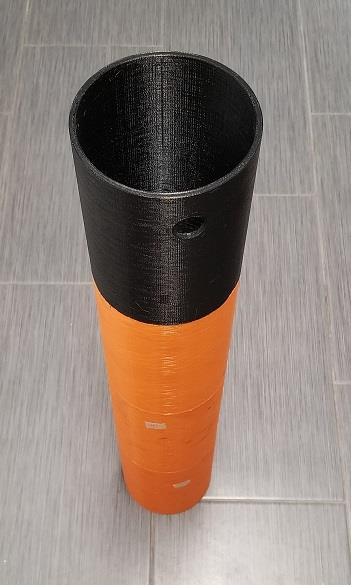
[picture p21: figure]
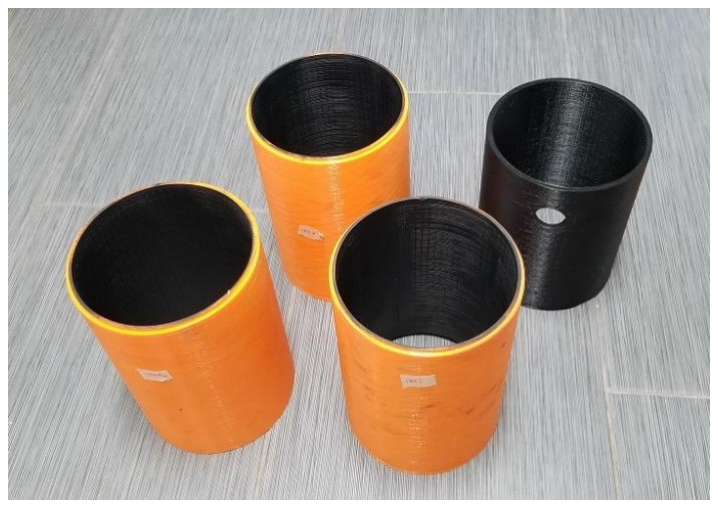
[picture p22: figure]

Figure 8. Segments after painting and assembled and glued together. (Top segment replaced because painting was too messy.)

The remaining instructions are the same, regardless of whether the tube was purchased, cut, and drilled, or if it was printed in segments and glued together. The pictures will show a combination of 80 mm with purchased tube and 114 mm with printed tube.

## Alignment

The purpose of aligning the mirrors is to ensure that the axis of the primary (and secondary) mirror is “looking” directly down the axis of the tube and not off to one side. If the mirrors are crooked, the telescope will still produce an image, but off-axis from perpendicular to the primary mirror. This creates optical aberration if the error is significant.

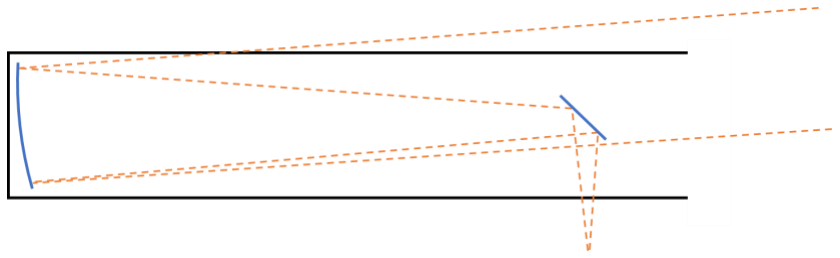
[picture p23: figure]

Figure 9. Severe misalignment will harm image quality. The primary mirror should be perpendicular to the axis of the tube.

While the alignment will affect image quality, it does not need to be extremely precise. It should not take more than about 5 minutes to align the primary mirror reasonably well.

## Mounting and Aligning the Primary

Before fixing the mirror in place, test fit the mirror mount onto the end of the tube. If it is the wrong size or if it can’t be tightened for some reason, it’s better to find out before the mirror is secured in place.

Note: if your mirror does not have a spot marked in the center, you will probably want to add one before mounting the mirror into the telescope. The “crosshairs” piece used for primary alignment also has a ring to assist locating the center of the primary mirror. Place it on the primary mirror such that the small gap is equal on all sides and then mark the center accordingly.

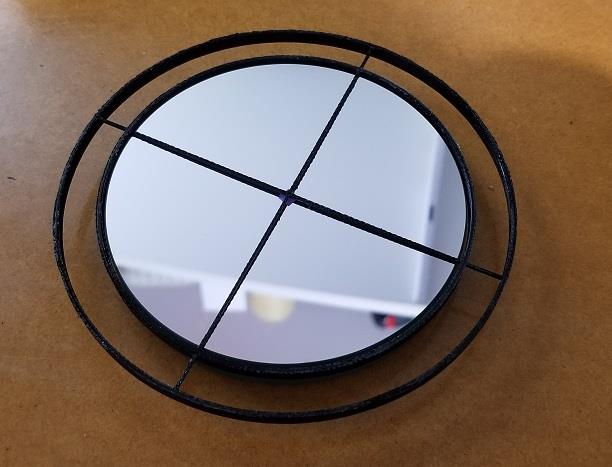
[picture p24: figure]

Figure 10. Use crosshairs piece to mark center of primary mirror.

The primary mirror is held to the mount by three spots of glue or tape, and the mount is clamped onto the end of the tube. Three optional adjustment screws allow spacing the mount slightly off of the end of the tube, to align the primary mirror, but I find it is easier to adjust without them.

After securing the mirror to the mount, use a screw to clamp the strap onto the end of the tube tight enough that it won’t fall off, but loose enough so some movement is still possible. Make a mark in the center of the mirror, and with a temporary ‘crosshairs’ mounted on the front end of the tube, adjust the primary mirror until the crosshairs, center mark, and the reflection of the crosshairs appear collinear. This ensures that the center of the mirror is pointing at the center of the front end of the tube.

This is much easier to see visually than it is to photograph. A 10-second video illustration can be seen at https://www.youtube.com/watch?v=JBTcHePyMpQ.

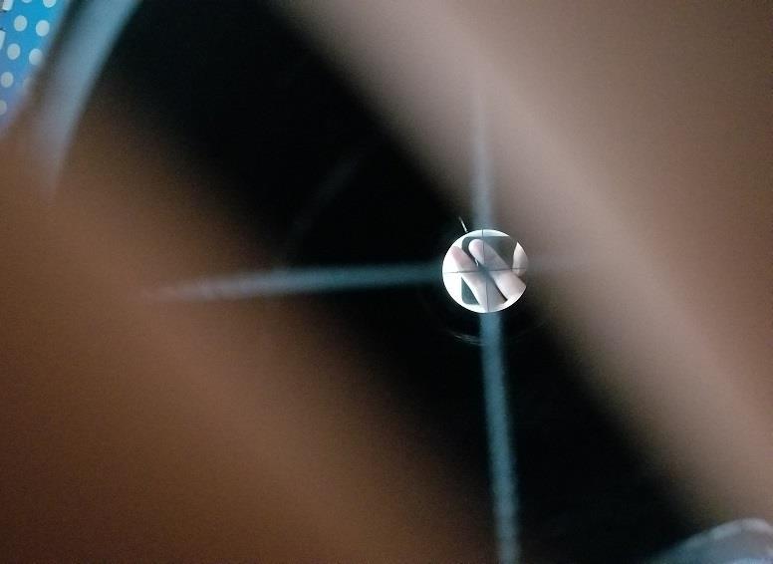
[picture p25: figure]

Figure 11. Camera, crosshairs, center of mirror, and reflection of crosshairs are all collinear.

There are three screw holes provided in the perimeter of the primary mirror mount that could be used for fine adjustment, but I found better success gently tapping the edge of the mirror mount to adjust it slightly on one side at a time.

After the adjustment, tighten the clamping screw to hold the mount securely in place, and after tightening, check again to validate that the alignment is still good.

## Mounting and Aligning the Secondary

As with the primary, test fit the secondary mirror mount onto the front end of the tube before securing the mirror in place.

The central post on the secondary mirror mount is slightly “short” to accommodate the thickness of the secondary mirror, placing the front surface of the mirror at the appropriate place. Because of this offset, together with the angled mount, it can be a little tricky to properly center the mirror on the mount.

To properly center the mirror, place tape such that the edge of the tape is across the short axis of the mirror. The mirror post has two ridges on the sides. Place the mirror such that the tape is in line with the ribs on both sides. This will ensure that the center of the mirror is properly centered within the tube.

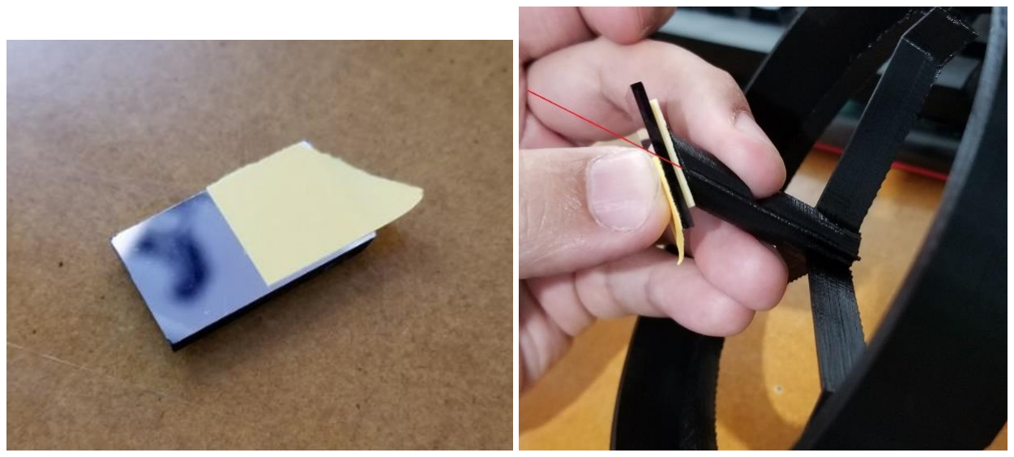
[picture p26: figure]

Figure 12. Tape on secondary mirror aligned axially with ribs on mount (illustrated with red line) to properly center

Use glue or tape to affix the secondary mirror onto the spider. If using glue, the mount has a feature to make it relatively easy to clamp the mirror in place while the glue sets.

After mounting the secondary onto the spider, mount the spider onto the front end of the telescope.

Orient the spider such that the secondary reflects out through the hole in the side. Gently tighten the clamping screw so the spider grips the front of the tube, but still allows adjustment.

Look through the hole in the side and make fine adjustments to the spider until you can see the reflection off the secondary, primary, and secondary again (and see your eye) in the reflection. As with the primary adjustment, there are holes for adjustment screws, but I found gently tapping the ring to be much easier. The spot in the center of the primary mirror should be coaxial with this view and it should be near the center of the hole.

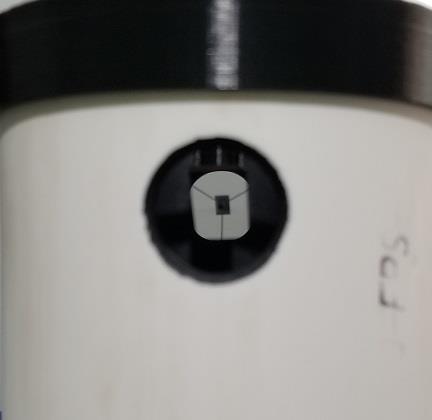
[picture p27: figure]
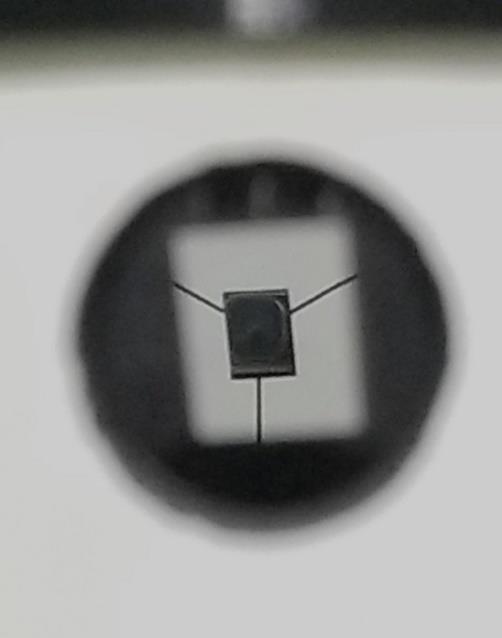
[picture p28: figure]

Figure 13. Alignment of secondary is complete when center of primary mirror appears coaxial with eye and center of hole

Tighten down the clamp on the spider, and after tightening, validate that the alignment is still good.

## Tripod Mount

Note: The tripod mount is far from ideal, and it is not recommended if you have another option. (A camera tripod is generally not very heavy or stable, so it tends to vibrate, and it is hard to move in small increments.) If nothing else is available, it can be used temporarily until a better one is developed.

To assemble, apply epoxy to the interior wall of the hexagonal recess, and then insert the ¼”-20 nut. Apply a bit more epoxy around the outside of the nut. The “floor” between the nut and the tripod is relatively thin because some tripods have short bolts. The epoxy adds strength so that the telescope has more support than just that thin layer of plastic.

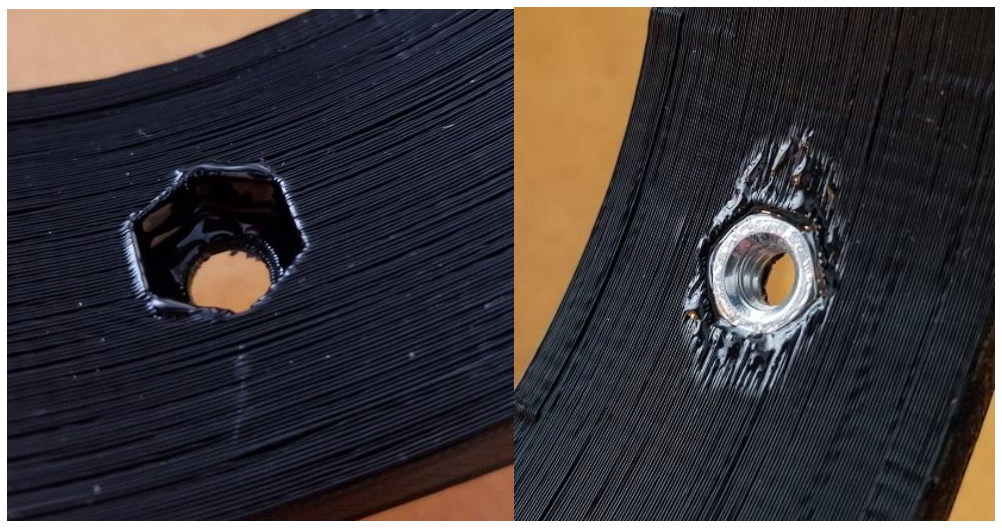
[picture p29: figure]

Figure 14. Epoxy secures nut to provide more strength than thin-wall plastic. (A small amount will do; the amount shown is too much and made a mess.)

Note: the tripod screw is not usually rigid enough to prevent unthreading by turning the entire telescope to the left or right. Use care when rotating the telescope to avoid accidentally unthreading the telescope from the tripod.

Tip: I have found it is generally very hard to move the tripod in small increments. One trick that seems to work is to grab the tip of one of the feet where it meets the ground and move it slightly. This changes the orientation of the telescope only slightly.

After the epoxy has set, the strap should be flexible enough to stretch to fit over the primary mirror mount, so no disassembly is needed to add or remove the tripod mount.

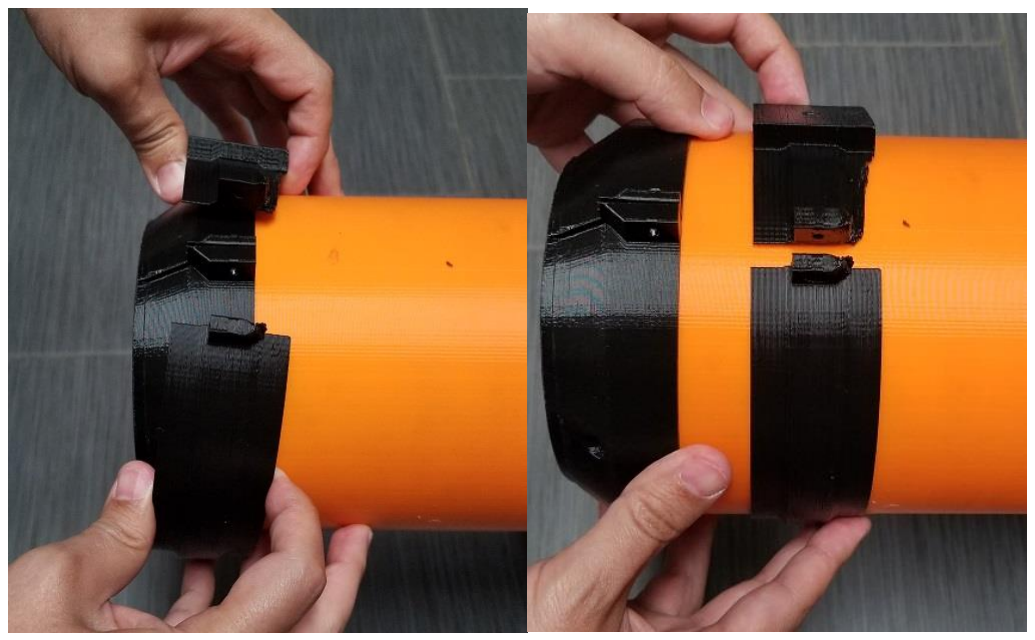
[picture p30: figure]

Figure 15. Stretch tripod mount strap to fit over the primary mirror mount.

Place the mount near the center of gravity of the telescope. Tighten down the clamp. Thread the tripod bolt into the trapped nut and secure.

## Viewer Mount (For Eyepiece or Other Accessories)

The Viewer Mount is attached to the tube at the hole in the side and allows mounting various accessories. As an interface it offers a 1.25-inch boss, 10 mm in length, with a flange behind it.

To attach the Viewer Mount to the telescope, simply slide it over the end of the tube, align with the hole, and tighten down with a screw. It should be flexible enough that it can be installed or removed without removing the secondary mirror mount.

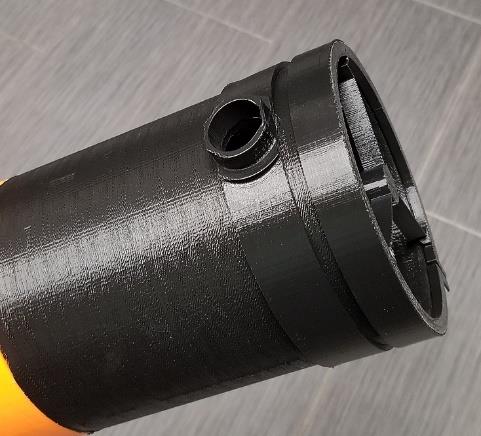
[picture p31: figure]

Figure 16. Viewer mount installed

## Eyepiece Mount

The eyepiece mount is extremely simple. Clamp one end firmly onto the boss of the viewer mount, and the other end onto the eyepiece. Gently tighten the clamp on the eyepiece, leaving it loose enough to allow movement by hand. Manually slide the eyepiece forward or back to get optimal focus, and then tighten the clamp on the eyepiece.

The length of the eyepiece mount is such that the image plane should be near the upper screw clamp, which is 72 mm away from the flange. However, small deviations in the assembly such as adjustments to align the primary or secondary mirror can influence the exact focus position.

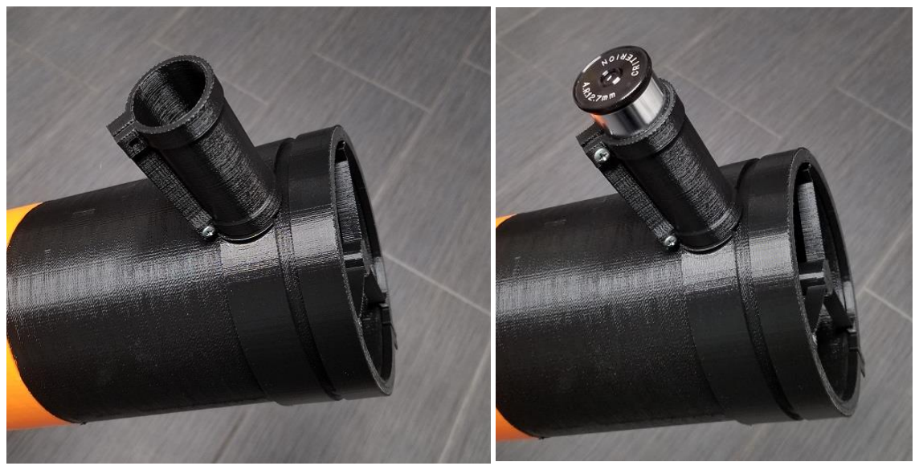
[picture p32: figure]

Figure 17. Eyepiece mount and installed eyepiece

## One Final Step

The last step is one of the most important: have fun! The image quality of this telescope will be as good or better than others of similar size, thanks to the somewhat fool-proof Newtonian configuration. Completing the project and exploring the night sky visually or through photography can be very rewarding. If you enjoy tinkering as much as astronomy, perhaps you can add an equatorial mount and clock drive. Maybe you can create a computerized tracking system or adapt an existing one.

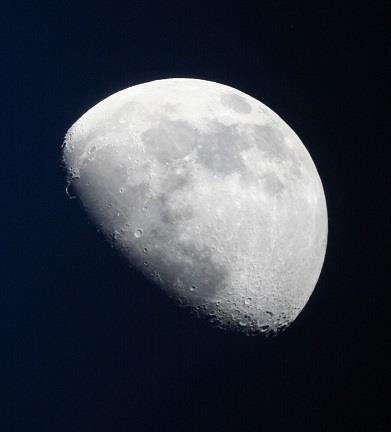
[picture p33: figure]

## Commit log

2022-07-13 first public commit
    [Canon_EF_mount_by_thenickdude.stl, F(star)P Newtonian.scad, accessories.scad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]
2022-07-13 add model files
    [Canon EF Mount.stl, D114F900 Aiming Reticle.stl, D114F900 Primary Aligner.stl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]
2022-07-15 bugfix (had occluded hole)
    [core_parts.scad]
2022-07-15 added "micro dobsonian" mount (untested, undocumented)
    [F(star)P Newtonian.scad, micro_dobs_mount.scad, unwin_modules.scad]
2022-07-15 added "micro dobsonian" mount (untested, undocumented) stl files
    [D114F900 Micro Dobs Print Layout.stl, D80F800 Micro Dobs Print Layout.stl]
2022-08-03 fix for large secondary mirrors (so the spider doesn't fall apart)
    [core_parts.scad]
